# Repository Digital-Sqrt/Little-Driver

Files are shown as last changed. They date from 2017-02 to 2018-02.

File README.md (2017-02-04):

# Little-Driver is covered by the Creative Commons Attribution-ShareAlike 3.0 Unported License.
please see the LICENSE test file for more information.

DOC -  All documents for construction, Manufacture, and use of the Little Driver.

Gerbrer -  all files necessary for board manufacturer.

MyLib.pretty - KiCad lib for the little Driver

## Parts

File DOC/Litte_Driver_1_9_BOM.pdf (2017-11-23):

# Little Driver 1.9

Reference | Value | Count Supplyer_Part_No | mfr_num | Manufacturer | Supplyer
Terminals | CONN_01X01 | 4 36-8197-ND | 8197 | Keystone Electronics | Digi-Key
PCB | Little DRIVER BOARD 1.9 | 1 Little DRIVER BOARD 1.9 | Little DRIVER BOARD 1.9 | PCB Way | Dirty Boards
Q1 | IRLS3034TRLPBF | 1 942-IRFR7540TRPBF | IRFR7540TRPBF | International Rectifer | Mouser
U1 | TLP182(BL-TPL,E | 1 757-TLP182(BL-TPLE | TLP182(BL-TPL,E | Toshiba Semiconductor and Storage | Mouser
CN1 | 6 Pin Headder | 1 538-15-91-2060 | 15912060 | Molex, LLC | Mouser
D3 | Led_Small | 1 941-CLM1BAKWCUAVB253 | CLM1B-AKW-CUAVB253 | CREE | Mouser
JP1 | Jumper_NC_Small | 1 517-9691020000DA | 969102-0000-DA | 3M | Mouser
R1 | 1.0K | 1 603-RC1206FR-071KL | RC1206FR-071KL | Yageo | Mouser
R4 | 1.69K | 1 603-RC1206FR-071K69L | RC1206FR-071K69L | Yageo | Mouser
R2 | 1.8K | 1 603-RC1206FR-071K8L | RC1206FR-071K8L | Yageo | Mouser
R5 | 3.6K | 1 603-RC1206FR-073K6L | RC1206FR-073K6L | Yageo | Mouser
R3 | 300 | 1 603-RC1206JR-07300RL | RC1206JR-07300RL | Yageo | Mouser

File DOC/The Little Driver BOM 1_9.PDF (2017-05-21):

Reference | Value | Count mfr_num | Manufacturer
Power+/- BED+/- | 8197 | 4 | 8197 | Keystone Electronics
Q1 | IRFR7540TRPBF | 1 | IRFR7540TRPBF | International Rectifer
U1 | TLP182(BL-TPL,E | 1 | TLP182(BL-TPL,E | Toshiba Semiconductor and Storage
CN1 | 6 Pin Headder | 1 | 15912060 | Molex, LLC
D3 | Led_Small | 1 | CLM1B-AKW-CUAVB253 | CREE
JP1 | Jumper_NC_Small | 1 | 969102-0000-DA | 3M
R1 | 1.0K | 1 | RC1206FR-071KL | Yageo
R4 | 1.69K | 1 | RC1206FR-071K69L | Yageo
R2 | 1.8K | 1 | RC1206FR-071K8L | Yageo
R5 | 3.6K | 1 | RC1206FR-073K6L | Yageo
R3 | 300 | 1 | RC1206JR-07300RL | Yageo

# Little Driver 1.9

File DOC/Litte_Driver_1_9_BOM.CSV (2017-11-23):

Little Driver 1.9
Reference | Value | Count | Supplyer_Part_No | mfr_num | Manufacturer | Supplyer | Supplyer_Link
Terminals | CONN_01X01 | 4 | 36-8197-ND | 8197 | Keystone Electronics | Digi-Key | http://www.digikey.com/products/en?keywords=36-8197-ND
PCB | Little DRIVER BOARD 1.9 | 1 | Little DRIVER BOARD 1.9 | Little DRIVER BOARD 1.9 | PCB Way | Dirty Boards | http://dirtypcbs.com/store/pcbs
Q1 | IRLS3034TRLPBF | 1 | 942-IRFR7540TRPBF | IRFR7540TRPBF | International Rectifer | Mouser | http://www.mouser.com/search/ProductDetail.aspx?R=0virtualkey0virtualkeyIRFR7540TRPBF
U1 | TLP182(BL-TPL,E | 1 | 757-TLP182(BL-TPLE | TLP182(BL-TPL,E | Toshiba Semiconductor and Storage | Mouser | http://www.mouser.com/ProductDetail/Toshiba/TLP182BL-TPLE/
CN1 | 6 Pin Headder | 1 | 538-15-91-2060 | 15912060 | Molex, LLC | Mouser | http://www.mouser.com/search/ProductDetail.aspx?R=0virtualkey0virtualkey15912060
D3 | Led_Small | 1 | 941-CLM1BAKWCUAVB253 | CLM1B-AKW-CUAVB253 | CREE | Mouser | http://www.mouser.com/search/ProductDetail.aspx?R=0virtualkey0virtualkeyCLM1B-AKW-CUAVB253
JP1 | Jumper_NC_Small | 1 | 517-9691020000DA | 969102-0000-DA | 3M | Mouser | http://www.mouser.com/search/ProductDetail.aspx?R=0virtualkey0virtualkey969102-0000-DA
R1 | 1.0K | 1 | 603-RC1206FR-071KL | RC1206FR-071KL | Yageo | Mouser | http://www.mouser.com/search/ProductDetail.aspx?R=0virtualkey0virtualkeyRC1206FR-071KL
R4 | 1.69K | 1 | 603-RC1206FR-071K69L | RC1206FR-071K69L | Yageo | Mouser | http://www.mouser.com/search/ProductDetail.aspx?R=0virtualkey0virtualkeyRC1206FR-071K69L
R2 | 1.8K | 1 | 603-RC1206FR-071K8L | RC1206FR-071K8L | Yageo | Mouser | http://www.mouser.com/search/ProductDetail.aspx?R=0virtualkey0virtualkeyRC1206FR-071K8L
R5 | 3.6K | 1 | 603-RC1206FR-073K6L | RC1206FR-073K6L | Yageo | Mouser | http://www.mouser.com/search/ProductDetail.aspx?R=0virtualkey0virtualkeyRC1206FR-073K6L
R3 | 300 | 1 | 603-RC1206JR-07300RL | RC1206JR-07300RL | Yageo | Mouser | http://www.mouser.com/search/ProductDetail.aspx?R=0virtualkey0virtualkeyRC1206JR-07300RL

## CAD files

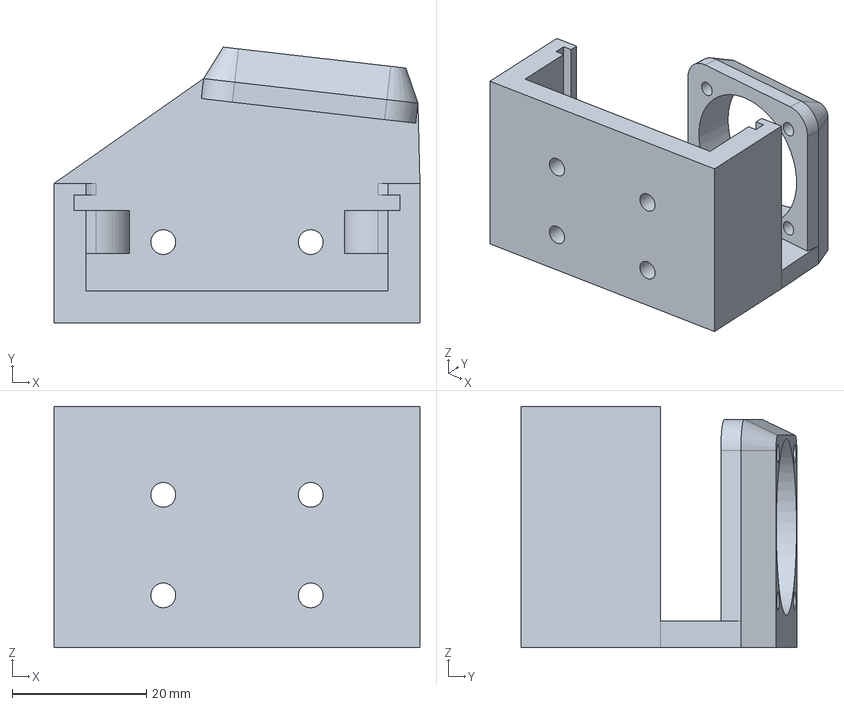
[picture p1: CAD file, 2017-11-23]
Mounting Brackets/Universal_Mounting_Bracket with Fan.stp
54.6 x 41.1 x 36.0 mm

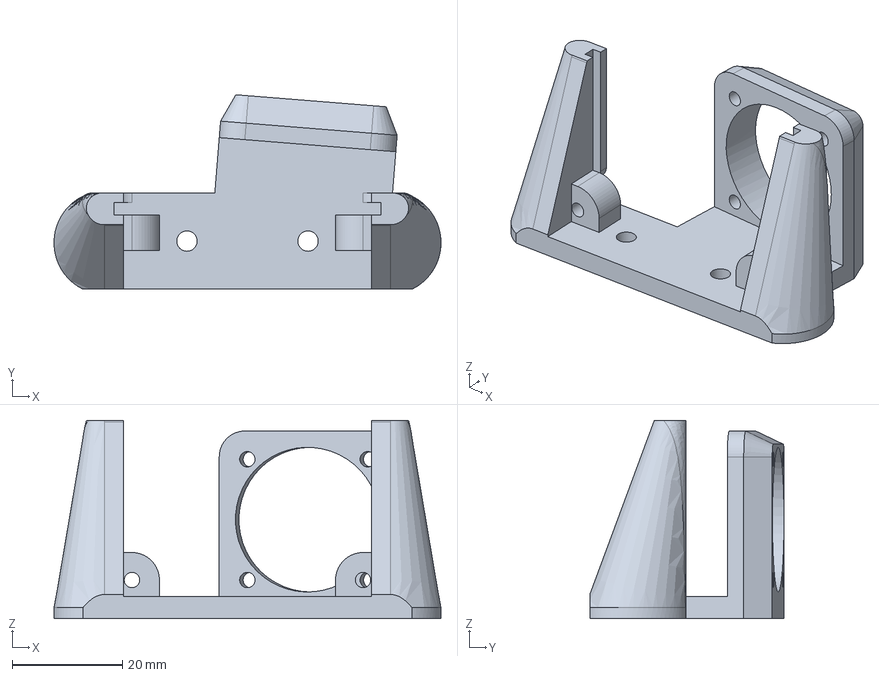
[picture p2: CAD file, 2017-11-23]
Mounting Brackets/Al_Ext_Mounting_Bracket with Fan.stp
70.3 x 35.3 x 36.0 mm

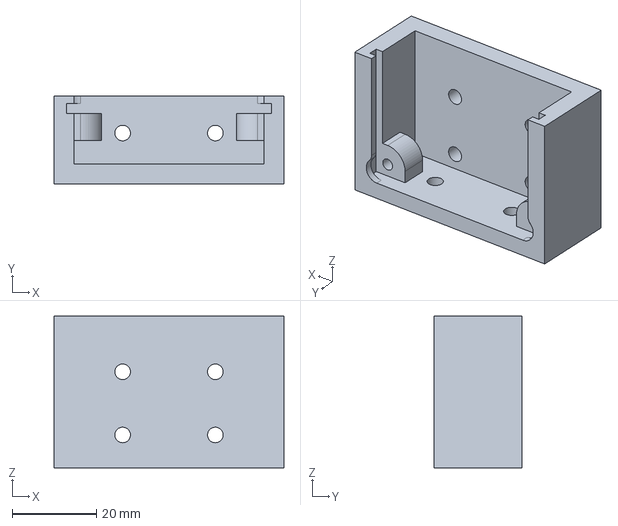
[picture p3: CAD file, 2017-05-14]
Mounting Brackets/Universal_Mounting_Bracket.stp
54.6 x 20.8 x 36.0 mm

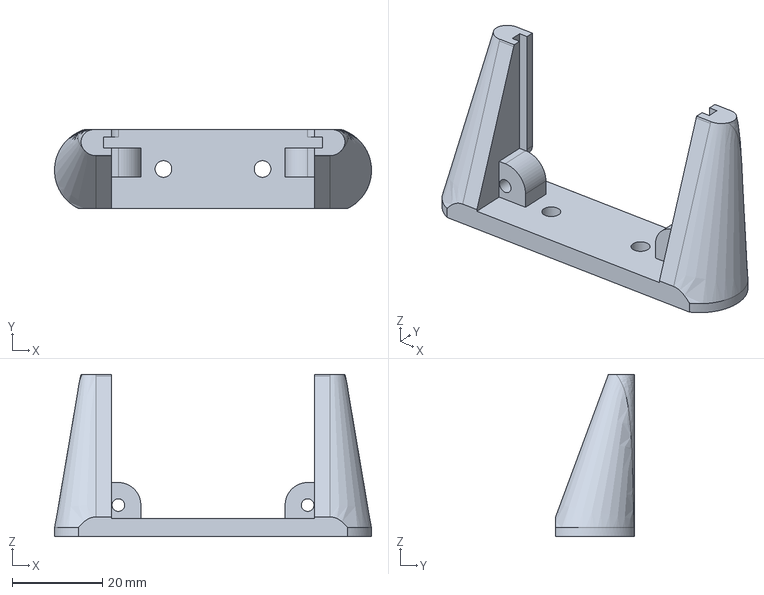
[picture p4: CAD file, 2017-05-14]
Mounting Brackets/Al_Ext_Mounting_Bracket.stp
70.3 x 17.5 x 36.0 mm

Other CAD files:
Mounting Brackets/Al_Ext_Mounting_Bracket with Fan.stl
Mounting Brackets/Al_Ext_Mounting_Bracket.stl
Mounting Brackets/Universal_Mounting_Bracket with Fan.stl
Mounting Brackets/Universal_Mounting_Bracket.stl

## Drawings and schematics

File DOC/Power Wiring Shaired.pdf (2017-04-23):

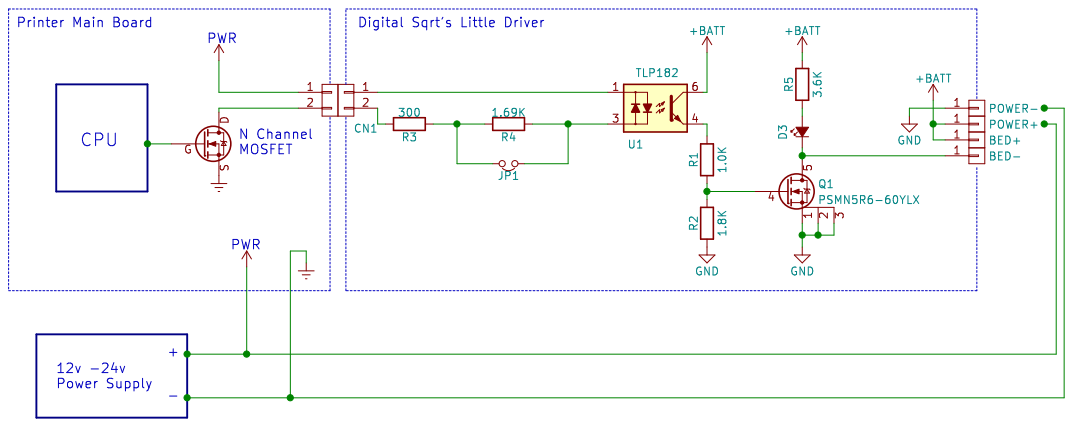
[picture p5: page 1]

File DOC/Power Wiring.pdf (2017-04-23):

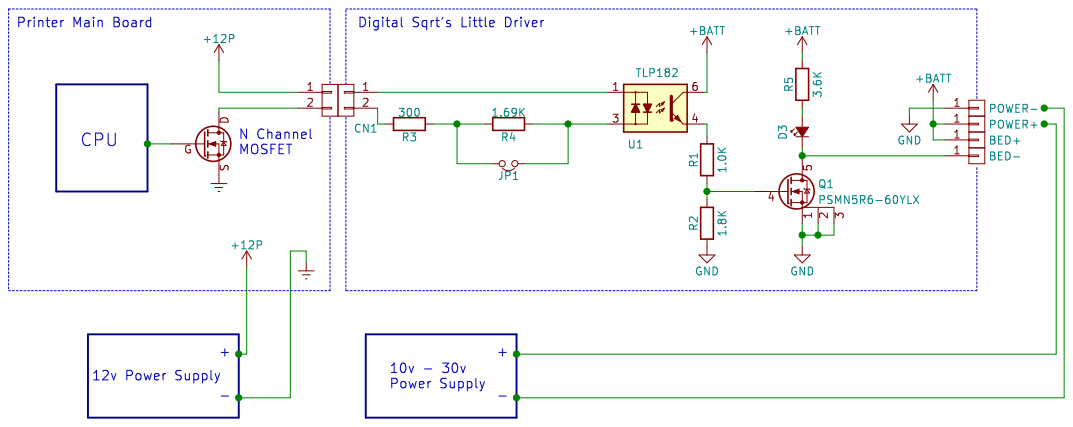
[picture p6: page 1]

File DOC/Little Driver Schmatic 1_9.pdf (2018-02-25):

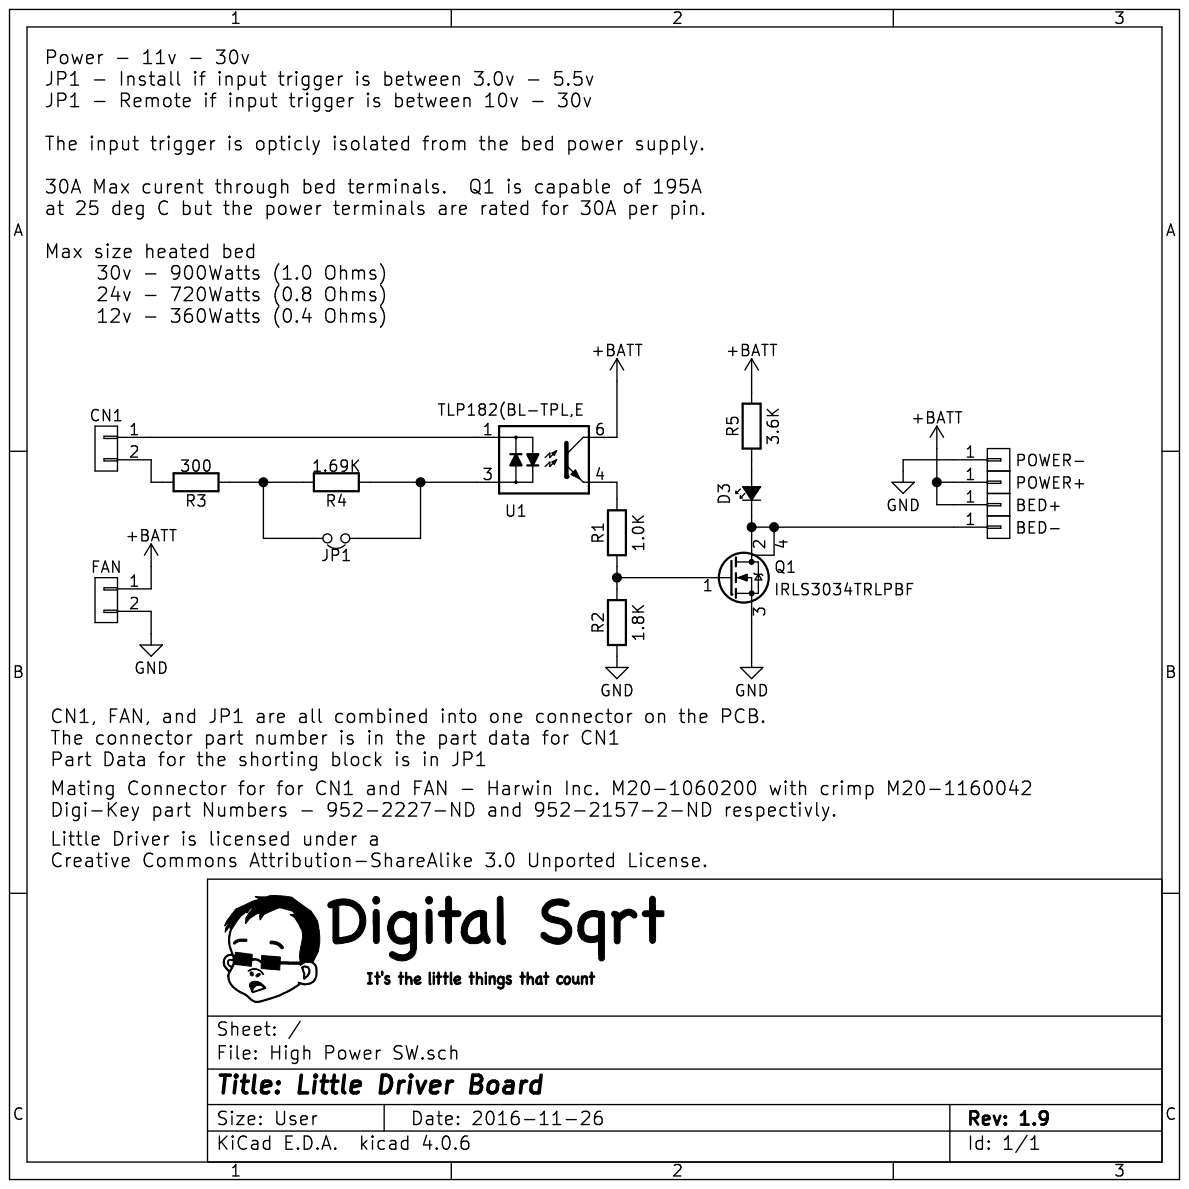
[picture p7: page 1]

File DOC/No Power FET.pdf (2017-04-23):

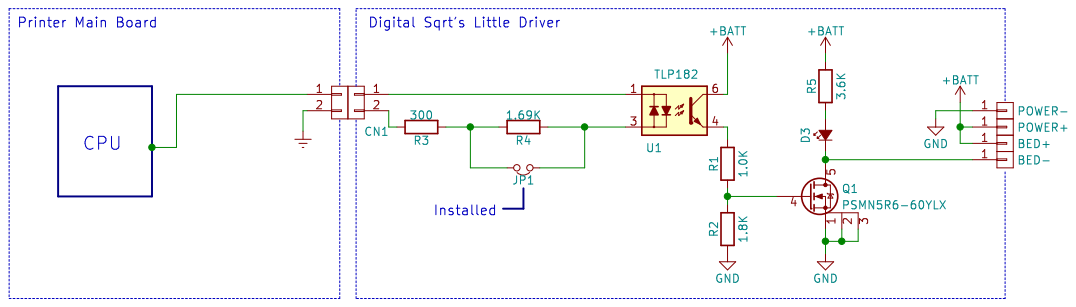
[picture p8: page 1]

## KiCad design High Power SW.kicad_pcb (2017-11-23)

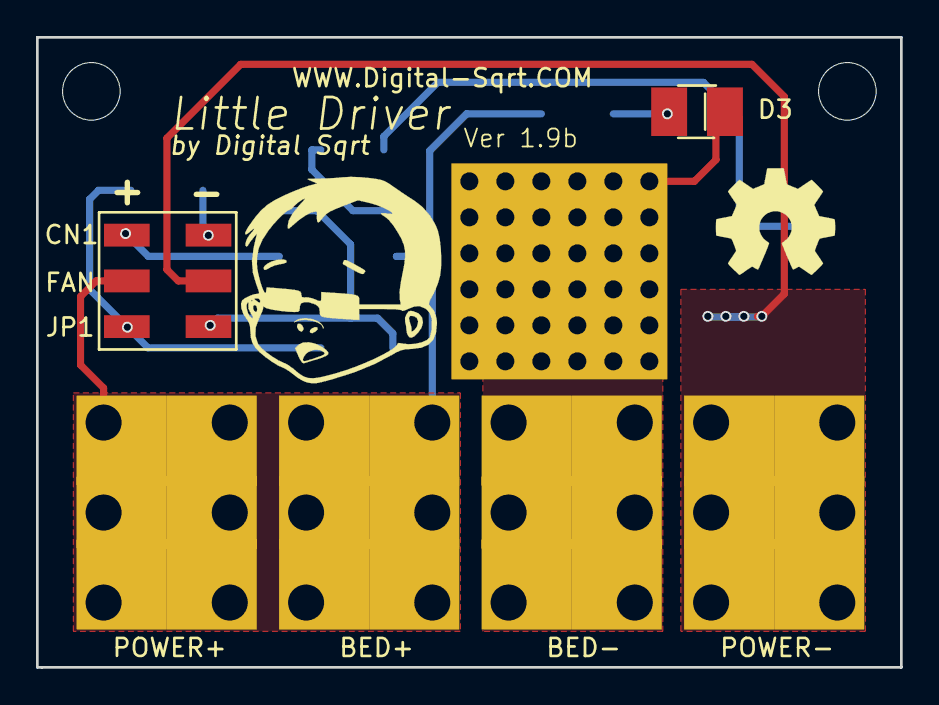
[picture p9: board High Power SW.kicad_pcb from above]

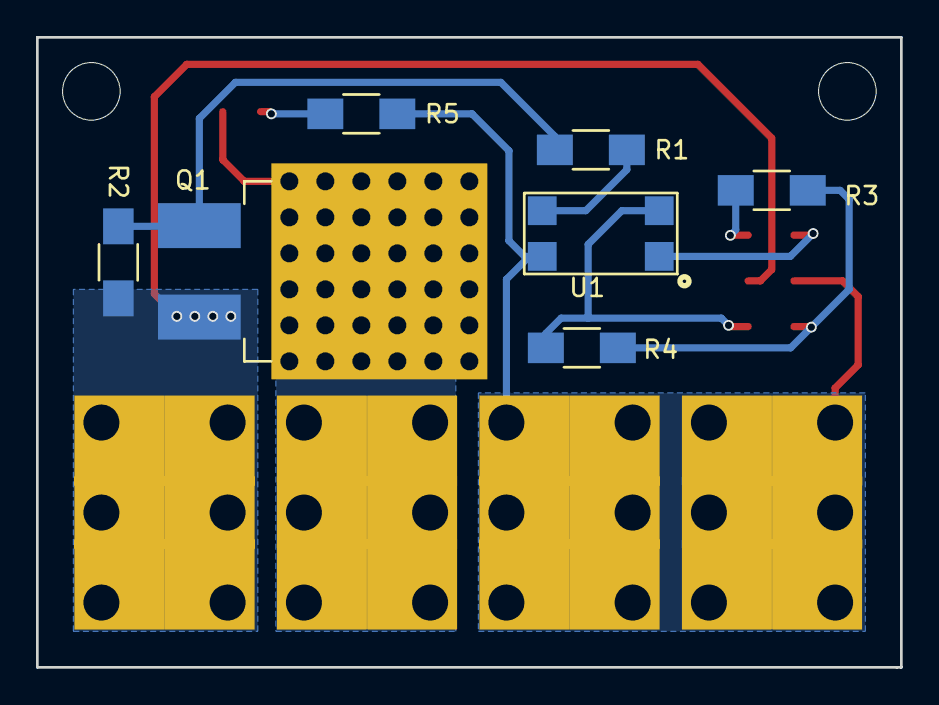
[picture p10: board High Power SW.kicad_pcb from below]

Board: 2 copper layers, 48.0 x 35.0 mm, 13 parts (7 on the bottom side), 10 nets.

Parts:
BED+: CONN_01X01; Keystone_terminal
BED-: CONN_01X01; Keystone_terminal
CN1: Jumper_NC_Small; 6pin_SMT_HEADER
D3: Led_Small; CREE_CLM1B_AKW_CUAVB253
POWER+: CONN_01X01; Keystone_terminal
POWER-: CONN_01X01; Keystone_terminal
Q1: IRFR7540TRPBF; TO-263-2Lead_(Small_Heat_Sink)
R1: 1.0K; R_1206_HandSoldering
R2: 1.8K; R_1206_HandSoldering
R3: 300; R_1206_HandSoldering
R4: 1.69K; R_1206_HandSoldering
R5: 3.6K; R_1206_HandSoldering
U1: PS2801C-1-A; TLP182

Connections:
+BATT: BED+.1, CN1.3, POWER+.1, R5.1, U1.6
GND: CN1.4, POWER-.1, Q1.3, R2.2
unnamed: BED-.1, D3.1, Q1.2, Q1.4
unnamed: CN1.1, U1.1
unnamed: CN1.2, R3.1
unnamed: D3.2, R5.2
unnamed: CN1.6, R4.2, U1.3
unnamed: CN1.5, R3.2, R4.1
unnamed: Q1.1, R1.2, R2.1
unnamed: R1.1, U1.4

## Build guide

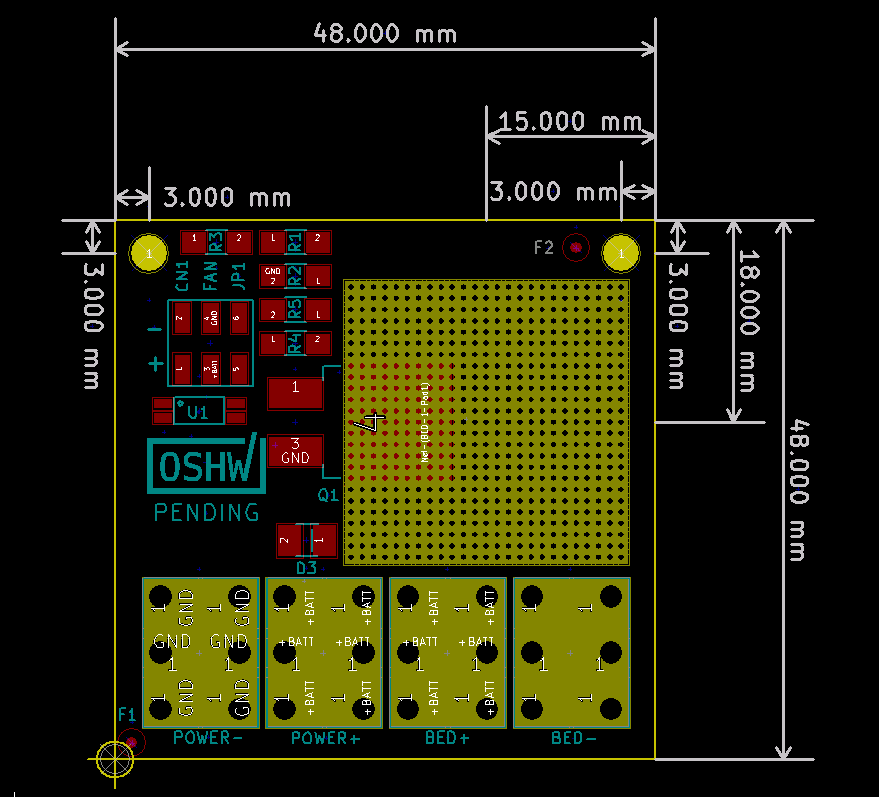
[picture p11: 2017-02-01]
DOC/Build Pic.PNG

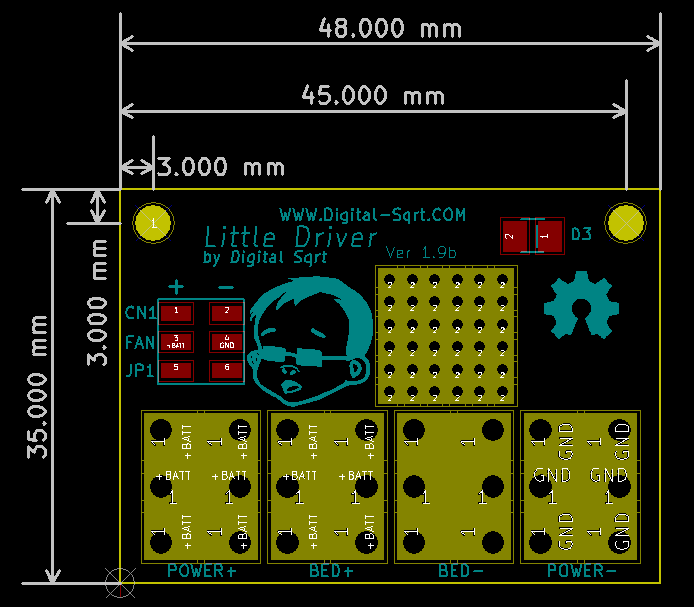
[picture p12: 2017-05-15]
DOC/Build 1_9.PNG

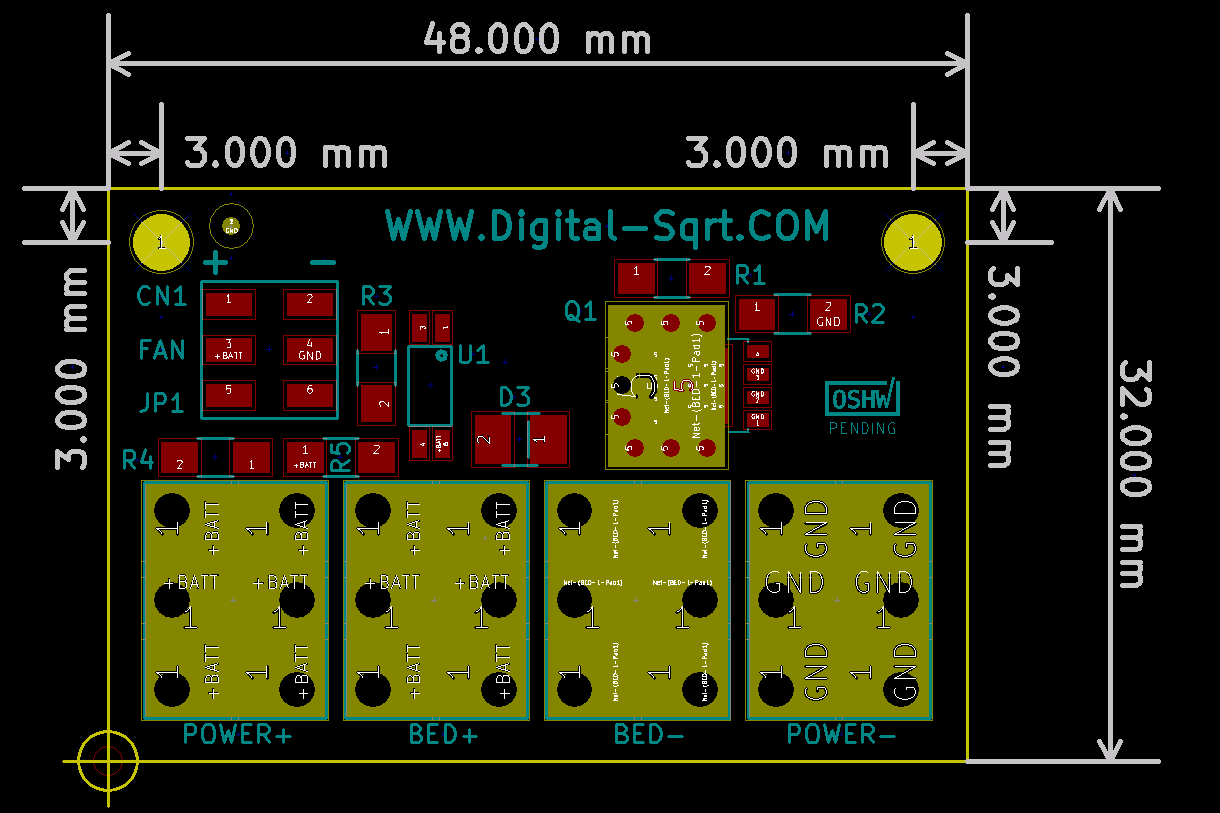
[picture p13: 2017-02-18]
DOC/Build Pic 1_7.PNG

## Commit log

2017-01-08 Add files via upload
    This is the 1.5v of the boar an the first commit.
    [High Power SW-B.Cu.gbr, High Power SW-B.Mask.gbr, High Power SW-B.SilkS.gbr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]
2017-01-11 Update to schmatic and BOM
    Updated R1 to 1.0K
    Added mating connector information to schematic
    [High Power SW.sch]
2017-01-11 Bug Fix
    Fixed Ki-Cad BOM generation error
    [High Power SW.sch, High Power SW_BOM.csv]
2017-01-19 Added Logo's to the schmatic and pcb
    Added a pending OSHWA Pending logo to the board
    Added Digital Sqrt Logo to board
    [High Power SW.kicad_pcb, High Power SW.sch]
2017-01-19 Added CC ref
    Little Driver is licensed under a
    Creative Commons Attribution-ShareAlike 3.0 Unported License.
    [High Power SW.sch]
2017-02-01 Update Manifacturing Files
    [High Power SW-B.Cu.gbr, High Power SW-B.Mask.gbr, High Power SW-B.SilkS.gbr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]
2017-02-01 Updated documentation
    [Little Driver BOM.xls]
2017-02-02 Updated BOM
    [Little Driver BOM.xls]
2017-02-04 Update for KiCost
    Updated Parts Lib so KiCost will work with KiCad
    [High Power SW.sch, High Power SW_BOM.csv]
2017-02-04 Clean Up
    [High Power SW_BOM.csv]
2017-02-05 Errors found in componet links in schmatic
    [High Power SW.sch]
2017-02-07 Maded Udates to silk
    [High Power SW-B.Cu.gbr, High Power SW-B.Mask.gbr, High Power SW-B.SilkS.gbr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]
2017-02-10 Updated Board
    Changed connector type
    [High Power SW.kicad_pcb, High Power SW.sch, High Power SW.xlsx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]
2017-02-11 Update Gerbr files
    [High Power SW-B.Cu.gbr, High Power SW-B.Mask.gbr, High Power SW-B.SilkS.gbr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]
2017-02-11 Update Gerbers
    [High Power SW-B.Cu.gbr, High Power SW-B.Mask.gbr, High Power SW-B.SilkS.gbr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]
2017-02-11 Update Gerbers One more time
    [High Power SW-B.Cu.gbr, High Power SW-B.Mask.gbr, High Power SW-B.SilkS.gbr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]
2017-02-11 Various Small updates
    [High Power SW.sch]
2017-02-12 Update to better parts
    UpDates to better parts for smaller board.
    [High Power SW.sch]
2017-02-12 Improved Board Size
    Made the board smaller
    [High Power SW-B.Cu.gbr, High Power SW-B.Mask.gbr, High Power SW-B.SilkS.gbr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]
2017-02-12 Reduced Board Size
    Cleaned up the board and made it smaller
    [High Power SW-B.Cu.gbr, High Power SW-B.Mask.gbr, High Power SW-B.SilkS.gbr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]
2017-02-13 Changed back to orginal connectors
    Changed back to orginal connectors. They are more sturdy.
    [High Power SW-B.Cu.gbr, High Power SW-B.Mask.gbr, High Power SW-B.SilkS.gbr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]
2017-02-13 Fixed Silk
    [High Power SW-B.Cu.gbr, High Power SW-B.Mask.gbr, High Power SW-B.SilkS.gbr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]
2017-02-13 Minor Tweeks
    [High Power SW-B.Cu.gbr, High Power SW-B.Mask.gbr, High Power SW-B.SilkS.gbr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]
2017-02-15 Updated Gerber Files
    [High Power SW-B.Cu.gbr, High Power SW-B.Mask.gbr, High Power SW-B.SilkS.gbr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]
2017-02-15 Updated Documents
    Updated documents, cleaned up files, added Brackets
    [Al_Ext_Mounting_Bracket.stl, Al_Ext_Mounting_Bracket.stp, High Power SW_BOM.csv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]
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2017-02-17 Added BOM for Ver 1.7
    [High Power SW_BOM 1_7.xlsm, Little Driver BOM 1_7.xls]
2017-02-17 Added win file
    [High Power SW_BOM 1_7.xlsm]
2017-02-18 Add Manufacturing Files
    [High Power SW-B.Cu.gbr, High Power SW-B.Mask.gbr, High Power SW-B.SilkS.gbr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]
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2017-02-18 Up Load the last of the Manufacturing files
    [Little Driver BOM 1_5.xls, Little Driver BOM 1_7.csv, Little Driver BOM 1_7.xls]
2017-02-23 Revert "Up Load the last of the Manufacturing files"
    This reverts commit ee7e60682b5b21ff10b9b6b08a1b8972e26ac501.
    [Little Driver BOM 1_5.xls, Little Driver BOM 1_7.csv, Little Driver BOM 1_7.xls]
2017-02-23 Fix a big GIT HUB screw up
    [Little Driver BOM 1_5.xls, Little Driver BOM 1_7.csv, Little Driver BOM 1_7.xls]
2017-02-23 Added OSHWA Number to board
    [High Power SW-B.Cu.gbr, High Power SW-B.Mask.gbr, High Power SW-B.SilkS.gbr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]
2017-04-01 added more mounting holes
    [High Power SW.kicad_pcb, High Power SW.sch]
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2017-04-01 improved hole size and location drawings
    [High Power SW.kicad_pcb]
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2017-04-02 updated documents for ver 1_8
    [Little Driver BOM 1_8.xls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]
2017-04-09 Update GERBER and Silk
    [High Power SW-B.Cu.gbr, High Power SW-B.Mask.gbr, High Power SW-B.SilkS.gbr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]
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2017-04-14 Make board 5x5
    5cm by 5cm boards are lower cost
    [High Power SW-B.Cu.gbr, High Power SW-B.Mask.gbr, High Power SW-Edge.Cuts.gbr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]
2017-04-14 Update for improved Manufacture
    [High Power SW-B.Cu.gbr, High Power SW-B.Mask.gbr, High Power SW-B.SilkS.gbr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]
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2017-04-21 Update opto footprint and add logos
    [High Power SW-B.Cu.gbr, High Power SW-B.Mask.gbr, High Power SW-B.SilkS.gbr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]
2017-04-21 Updated Bracket files for a 50mm Board
    [Al_Ext_Mounting_Bracket.stl, Al_Ext_Mounting_Bracket.stp, Universal_Mounting_Bracket.stl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]
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2017-04-21 fixed Gerbers
    [High Power SW-B.Cu.gbr, High Power SW-B.Mask.gbr, High Power SW-B.SilkS.gbr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]
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2017-04-22 Updated bill of materials
    [High Power SW.sch]
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2017-04-28 Update Board Design based on feedback
    [Al_Ext_Mounting_Bracket.stl, Al_Ext_Mounting_Bracket.stp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]
2017-04-28 Cleaned up Gerber Data
    [High Power SW-B.Cu.gbr, High Power SW-B.Mask.gbr, High Power SW-B.SilkS.gbr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]
2017-05-02 Compleat Redesign
    [High Power SW-B.Cu.gbr, High Power SW-B.Mask.gbr, High Power SW-B.SilkS.gbr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]
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2017-05-11 Fixed issues with manufacture
    [High Power SW-B.Cu.gbr, High Power SW-B.Mask.gbr, High Power SW-B.SilkS.gbr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]
2017-05-13 Fixed Buggs found in Prototypes
    [High Power SW-B.Cu.gbr, High Power SW-B.Mask.gbr, High Power SW-B.SilkS.gbr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]
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2017-05-29 fixed issue with the links
    [High Power SW.sch]
2017-06-24 Add Bill of Materials
    [Litte_Driver_1_9_BOM.CSV]
2017-11-23 Updated Brackets.
    The fans would hit JP1, they have been moved.
    [Al_Ext_Mounting_Bracket with Fan.stl, Al_Ext_Mounting_Bracket with Fan.stp, Universal_Mounting_Bracket with Fan.stl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]
2017-11-23 Improve FET Design
    Add new FET
    [High Power SW.sch]
2017-11-23 Update Board for Better FET
    [High Power SW.sch]
2017-11-23 updated doc
    Updated board Docs
    [High Power SW.kicad_pcb]
2017-11-23 Documentation Updates
    Documentation Updates
    [Litte_Driver_1_9_BOM.CSV]
2018-02-25 Fixed error in schmatic
    The opto isolator had the incorrect part number
    [High Power SW.sch]
